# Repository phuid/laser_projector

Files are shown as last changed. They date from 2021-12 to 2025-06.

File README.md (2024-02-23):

# Raspberry Pi RGB laser projector
A vector laser projector with an easy to understand UI.\
UI includes:
- integrated display control with a rotary encoder,
- web server on the local network
- discord bot accesible when the RPi is online

## table of contents
- [Raspberry Pi RGB laser projector](#raspberry-pi-rgb-laser-projector)
  - [table of contents](#table-of-contents)
  - [thesis](#thesis)
  - [how to install](#how-to-install)
  - [supported projection file formats](#supported-projection-file-formats)
  - [hw](#hw)
    - [galvos](#galvos)
      - [DAC - mcp4822](#dac---mcp4822)
      - [amps - TL082](#amps---tl082)
    - [laser](#laser)
    - [LCD + encoder](#lcd--encoder)
  - [sw](#sw)
    - [communication](#communication)
    - [lasershow](#lasershow)
    - [UI](#ui)
    - [web\_ui](#web_ui)
    - [discord\_bot](#discord_bot)
    - [wifi\_manager](#wifi_manager)
    - [comms format](#comms-format)
      - [lasershow comms](#lasershow-comms)
        - [basic commands:](#basic-commands)
        - [responses:](#responses)
      - [wifi\_manager comms](#wifi_manager-comms)

## thesis
I wrote a whole thesis in [czech](https://en.wikipedia.org/wiki/Czech_Republic) language about this project. It is available in [this repository](https://github.com/phuid/laser_projector-thesis) [(direct link to the pdf file)](https://github.com/phuid/laser_projector-thesis/blob/master/text.pdf).

## how to install

```bash
git clone https://github.com/phuid/laser_projector.git
cd laser_projector
bash install.sh
```
this script installs all the dependencies of my programs and sets up the RaspberryPi to start all the programs on boot using [pm2](https://pm2.keymetrics.io/).

## supported projection file formats
The projector can read and project **.ild** and (much more popular) **.svg** file formats.
**.ild** files can be generated using specialised software like [laserworld showeditor](https://www.showeditor.com/en).
**.svg** files from any editor are internally converted to **.ild** using [this svg2ild.py script](https://github.com/marcan/openlase/blob/master/tools/svg2ild.py) from [gh/marcan/openlase](https://github.com/marcan/openlase)

## hw
My plans include battery power, usually galvos come with a power supply and powering the laser isn't that hard using a step-up. My module takes around 0.45A @ 9V. Make sure you dont brick your pi by taking its power. Raspberry Pis often don't take it well when an undervoltage occurs on their 5V line and they certainly aren't made to power anything more than an LED from their 3.3V PS.

### galvos
take -10 to +10V differential signal between to lines (base and inverted),
The DAC + opamps circuit which generates this signal is nicely described in [this article](https://www.instructables.com/Arduino-Laser-Show-With-Real-Galvos/).
My implemetation of it in kicad files can be found in [pcb/kicad](pcb/kicad).

#### DAC - mcp4822
DAC controlled by the RPi creates an analog signal between 0 and 5V.

#### amps - TL082
TL082 from texas instruments, each channel has one chip, each chip has two op amps.
One opamp inverts and modifies the signal based on the potenciometers (getting the inverted ILDA signal),
Second opamp inverts it again for the base ILDA signal

### laser
rgb laser module from https://www.laserlands.net/diode-laser-module/rgb-combined-white-laser-module/11010003.html
requires 8.5-12V power
takes 35kHz TTL / PWM on 3 pins, these pins are connected directly to the raspberry pi

pin connections between the laser module and RPi
|LASER|RPi|
|---|---|
|red|GPIO22|
|green|GPIO27|
|blue|GPIO17|

### LCD + encoder
Any 20x4 LCD with an I2C backpack + any rotary encoder with a button 
LCD connections:
|LCD|RPi|
|---|---|
|Vcc|5V|
|GND|GND|
|SCK|GPIO3|
|SDA|GPIO2|
|backlight|GPIO18|

encoder connections:
|encoder|RPi|
|---|---|
|A|GPIO5|
|common|GND|
|B|GPIO6|
|button1|GND|
|button1|GPIO13|

## sw
2 backend programs (lasershow *(c++)* + wifi_manager *(node.js)*) and 3 frontend programs (UI *(c++)* + web_ui *(node.js)* + discord_bot *(node.js)*)

### communication
each backend has its pub/sub sockets
lasershow publishes to `tcp://localhost:5556` and receives commands from `tcp://localhost:5556`
wifi_manager publishes to `tcp://localhost:5558` and receives commands from `tcp://localhost:5559`

### lasershow
- backend program that takes care of the actual projecting through controlling the galvos and the laser module

### UI
- allows control of backend programs through the built-in LCD and encoder

### web_ui
- allows control of backend programs through a web interface available on the local network

### discord_bot
- allows control of backend programs through a discord bot

### wifi_manager
- allows switching between three modes of wifi:
  - wifi off (`stealth`)
  - wifi on (`wifi`) -- RPi wifi on and trying to connect to known nearby networks
  - access point (`hotspot`) -- RPi wifi on transmitting its own wifi which other devices can connect to

### comms format
#### lasershow comms

lasershow executable takes commands **from all UI processes** through a **ZeroMQ TCP socket**
command format
`COMMAND` + ` ` + `ARG1` + ` ` + `ARG2` + ` ` + ` ` + `ARG4`
-> parse with a simple while loop lol no need for fancy functions

##### basic commands:
any process can send a command into the socket and all processes will read responses from lasershow executable
- `PROJECT` args: `<filename>`
  - `<filename>` must have extension `.ild`<!-- or `.lpc`(laserprojector_custom) --> otherwise error `INVALID_ARG`
- `STOP` (no args)
- `PAUSE` (no args)
- `GAME` args: `<game_name>`
  - `game_name` is any of the following ``//TODO: game names (not yes implemented)
- `PRESS` (no args), only handled if game is running
- `RELEASE` (no args), only handled if game is running
- `OPTION` args: `<mode>` `<option_name>` `<value>`
  - `mode`: any of `write`/`read`/`reset`
  - `option_name`: any of the following
    - `progress`
    - `current_frame` - if a projection is active, this will seek to the defined frame of the projection, must not exceed number_of_frames (every pos info gives this argument)
    - `point_delay`
    - `target_frame_time`
    - `repeat`
    - `trapeziod_horizontal`
    - `trapeziod_vertical`
  - `value` only read when using `write` parameter

##### responses:
lasershow exec can write to the socket at any time
- `ERROR: <e> <details>`:
  - `e`: any of the following; returned if received command couldn't be parsed correctly
    - `E2BIG`: too many arguments (option read/reset command probably includes value argument)
    - `EINVAL`: invalid argument (typo in argument or project filename probably has wrong extension)
    - `ENOENT`: file doesn't exist
    - `INVALID_CMD`: probably typo in a command
    - `OTHER`
  - `details`: if error type supports it, details will be included
- there is no success message
- `INFO: <details>`
  - details - one of following:
    - `OPTION <name> <val>`
      - name: name of option being changed; *any of*:
        - `point_delay`
        - `repeat`
        - `target_frame_time`
        - `trapezoid_horizontal`
        - `trapezoid_vertical`
      - val: numeric (float) value of the option
    - `STOP`
    - `PAUSE <val>`
      - val: 1 - paused, 0 - not paused
    - `PROJECT <filename>`
      - filename: filename of the file being projected
    - `POS <pos> OF <max>`
      - pos: position of coursor in projected file
      - max: size of projected file
- `DISPLAY: <text>`: client shall display text to the user and hide it when a new command comes or when user sees it
- `ALERT: <text>`: client shall display text to the user and only hide it and process following commands after user sees the alert

#### wifi_manager comms
takes following commands
- `read`: prints out following parameters:
  - `wifi_setting: <stealth|wifi|hotspot>`
  - `wifi_ssid: <SSID>`: SSID as returned by `iwgetid --raw` or `iw dev` in case hotspot is active
  - `mode_raw: <MODE_RAW>`: MODE_RAW (0-7) as returned by `iwgetid --mode --raw`
  - `mode: <MODE>`: MODE based on MODE_RAW; possible outputs: `Auto|Ad-Hoc|Managed|Master|Repeater|Secondary|Monitor|Unknown/bug`

- `write <stealth|wifi|hotspot>`
  - `stealth`: wifi off
  - `wifi`: connect to nearby known networks
  - `hotspot`: create new network, raspberry pi becomes the access point

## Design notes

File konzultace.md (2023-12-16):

# konzult

## hw
- rpi
- galva <- DAC 
- laser rgb <- DAC / TTL

### UI
- enkoder + OLED
- web_ui
- discord_bot

github haberturdeur /tet

## todo

- socket misto pipe (2.p.)

### done

- static encoder.hpp + cpp
- reference misto pointeru v menu_interract
- main menu def - constcast / std::string.c_str()

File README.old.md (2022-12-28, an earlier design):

# Raspberry Pi laser projector

not finished, not tested

## Table of contents

- [Raspberry Pi laser projector](#raspberry-pi-laser-projector)
  - [Table of contents](#table-of-contents)
  - [Tutorial](#tutorial)
    - [Hardware](#hardware)
    - [Software](#software)
      - [installing whole system from my disk image](#installing-whole-system-from-my-disk-image)
      - [installing executables from my repo source code](#installing-executables-from-my-repo-source-code)
        - [cloning my repository and installing manually](#cloning-my-repository-and-installing-manually)
    - [Hardware construction](#hardware-construction)
  - [What my code does - what happens when your RPI starts](#what-my-code-does---what-happens-when-your-rpi-starts)
  - [Progress (everything you need is above this part)](#progress-everything-you-need-is-above-this-part)
    - [Software progress](#software-progress)
    - [Hardware progress](#hardware-progress)

## Tutorial

*RPI = Raspberry Pi*
### Hardware

### Software

there are two ways of doing this, you can

- [install from a disk image](#installing-whole-system-from-my-disk-image)
  - much much easier
  - you need to download a 4GB file

  or

- [install the executables and dependencies yourself (download source)](#installing-executables-from-my-repo-source-code)
  - objectively harder
  - needs node and npm installed (i think node comes with the normal version of RPI OS preinstalled but i was using RPI OS Lite, since i needed to fit all this into a small .img file and was using a 4GB SD card)
    - **discord.js library requires node v16.6.0 or newer and npm v8.3.0 or newer**
    - using [Node version manager](https://github.com/nvm-sh/nvm) - [install tutorial](https://github.com/nvm-sh/nvm#installing-and-updating), [usage](https://github.com/nvm-sh/nvm#usage)
      - much more flexible
      - you can choose node and npm version
    - [download and install node and npm binaries yourself](https://www.makersupplies.sg/blogs/tutorials/how-to-install-node-js-and-npm-on-the-raspberry-pi)

#### installing whole system from my disk image

#### installing executables from my repo source code

##### cloning my repository and installing manually

download my code run these in the RPIs terminal

```console
git clone https://github.com/phuid/laser-projector.git
```

change your current working directory

```console
cd laser-projector
```

Install lasershow executable from [rpi-lasershow](https://github.com/tteskac/rpi-lasershow) project made by [@tteskac](https://github.com/tteskac)

enter rpi-lasershow dir

```console
cd rpi-lasershow
```

make the executable

```console
make
```

copy the executable to the main dir

```console
cp lasershow ../
```

exit the rpi-lasershow dir

```console
cd ..
```

at this point you dont really need the rpi-lasershow directory so you can delete it

it doesnt hurt to keep it at all this is just a possibility

```console
rm -r rpi-lasershow
```

now install the system dependencies and WiringPi and pm2
//TODO

then install all the node dependencies and set up pm2

enter every dir where a separate node server is gonna be located (**.**, **./discord_bot**, **./wifi_manager**) and intall its depencencies, then leave it

```console
npm i child_process http formidable fs path && pm2 start laser_projector-web-ui.js
``` 

**MAKE SURE, YOU CONNECTED THE AP/STEALTH/WIFI SWITCH CORRECTLY BEFORE STARTING THE wifi_manager.js SCRIPT, I DID IMPLEMENT A FAILSAFE, BUT EVEN I DONT REALLY TRUST IT (the failsafe includes the script not running if a pin isnt connected)

//TODO what fkin pin

```console
cd wifi_manager && npm i onoff child_process fs && pm2 start wifi_manager.js && cd ..
```

```console
cd discord_bot && npm i discord.js @discordjs/builders @discordjs/rest child_process path request fs
```

while you still are in **./discord_bot** you should put your bot credentials into config.json file and register the bots commands by running the deploy_commands.js script

```console
nano config.json
```

```console
node ./deploy_commands.js
```

now configure the pm2 autostart

```console
pm2 start discord_bot.js
```

then you can exit it

```console
cd ..
```

now check that all the pm2 services are online

```console
pm2 status
```

there should be three processes online like you can see below

//TODO

###### possible errors
if wifi manager isn't running and `pm2 logs wifi_manager` displays following
```js
/home/pi/laser_projector/wifi_manager/node_modules/bindings/bindings.js:121
        throw e;
        ^

Error: libnode.so.72: cannot open shared object file: No such file or directory
    at Object.Module._extensions..node (node:internal/modules/cjs/loader:1249:18)
    at Module.load (node:internal/modules/cjs/loader:1043:32)
    at Function.Module._load (node:internal/modules/cjs/loader:878:12)
    at Module.require (node:internal/modules/cjs/loader:1067:19)
    at require (node:internal/modules/cjs/helpers:103:18)
    at bindings (/home/pi/laser_projector/wifi_manager/node_modules/bindings/bindings.js:112:48)
    at /home/pi/laser_projector/wifi_manager/node_modules/epoll/epoll.js:7:31
    at Object.<anonymous> (/home/pi/laser_projector/wifi_manager/node_modules/epoll/epoll.js:15:3)
    at Module._compile (node:internal/modules/cjs/loader:1165:14)
    at Object.Module._extensions..js (node:internal/modules/cjs/loader:1219:10) {
  code: 'ERR_DLOPEN_FAILED'
}
```
run `cd wifi_manager/ && npm clean-install` in the laser_projector directory

### Hardware construction

this part is not gonna be added untill around Febuary 2022, since that's when my brother is gonna start working on modeling the case and when we are gonna buy the Galvos and all other components and put them together.

## What my code does - what happens when your RPI starts

1. pm2 starts ./laser_projector-web_ui.js, ./wifi_manage/wifi_manager.js and ./discord_bot/discord_bot.js

2. wifi_manager configures the wlan0 module based on the AP/stealth/wifi switch  

    *grounded = connected to ground*  
    *AP = access point (hotspot)*  

    1. if neither of pins (GPIO/BCM pin 6, GPIO/BCM pin 5) are grounded my code runs `sudo ifconfig wlan0 down`  
    and  
    `sudo systemctl disable hostapd dnsmasq`  
    else it runs just  
    `sudo ifconfig wlan0 up`

    2. if pin 6 is grounded it starts configuring an AP on the RPI

        1. `sudo systemctl enable hostapd dnsmasq`

        2. removes comment from the last section of my `/etc/dhcpcd.conf` file (add following to the file)  

                interface wlan0
                    static ip_address=192.168.4.1/24
                    nohook wpa_supplicant

        3. reboots the RPI

        4. every time it starts (on boot) it checks if hostapd.service is enabled
            - if it is NOT, it enables it in steps 1., 2. and 3. above
            - if it is, it continues

        5. `sudo ifdown wlan0`

        6. `sudo systemctl start dnsmasq`

        7. `sudo hostapd -B /etc/hostapd/hostapd.conf`

        8. `sudo systemctl reload dnsmasq`

    3. if pin 5 is grounded it starts configuring default wifi connection on the RPI
        1. `sudo systemctl stop hostapd dnsmasq`

        2. checks, if RPI is already connected to a wifi
            - if it is it breaks and doesnt continue
            - if it isn't it continues with steps 

        3. `sudo systemctl disable hostapd dnsmasq`

        4. comments out the last section of my `/etc/dhcpcd.conf` file

                #interface wlan0
                    #static ip_address=192.168.4.1/24
                    #nohook wpa_supplicant

        5. reboots the RPI and doesn't need to do anything after

## Progress (everything you need is above this part)

### Software progress

### Hardware progress

for some reason my pi saw the voltage on some pins as HIGH when they werent connected to anything, so i had to detect, wht pins were grounded instead of wht pins were taking power

still powered by usb
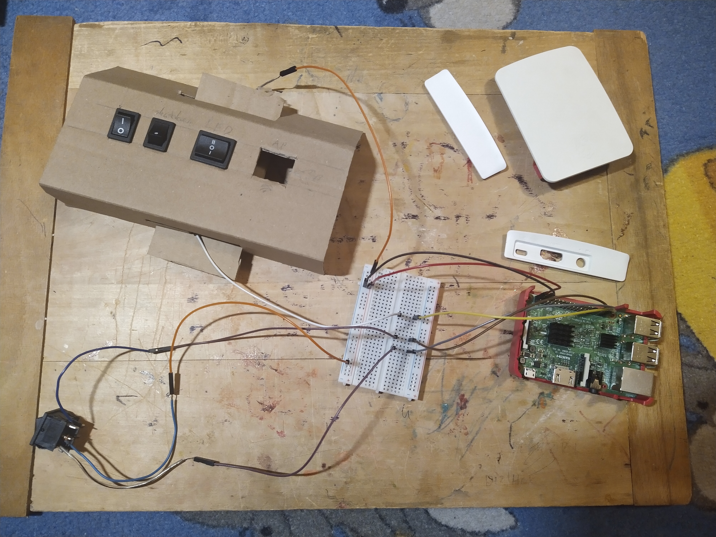
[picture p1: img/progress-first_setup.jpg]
first setup

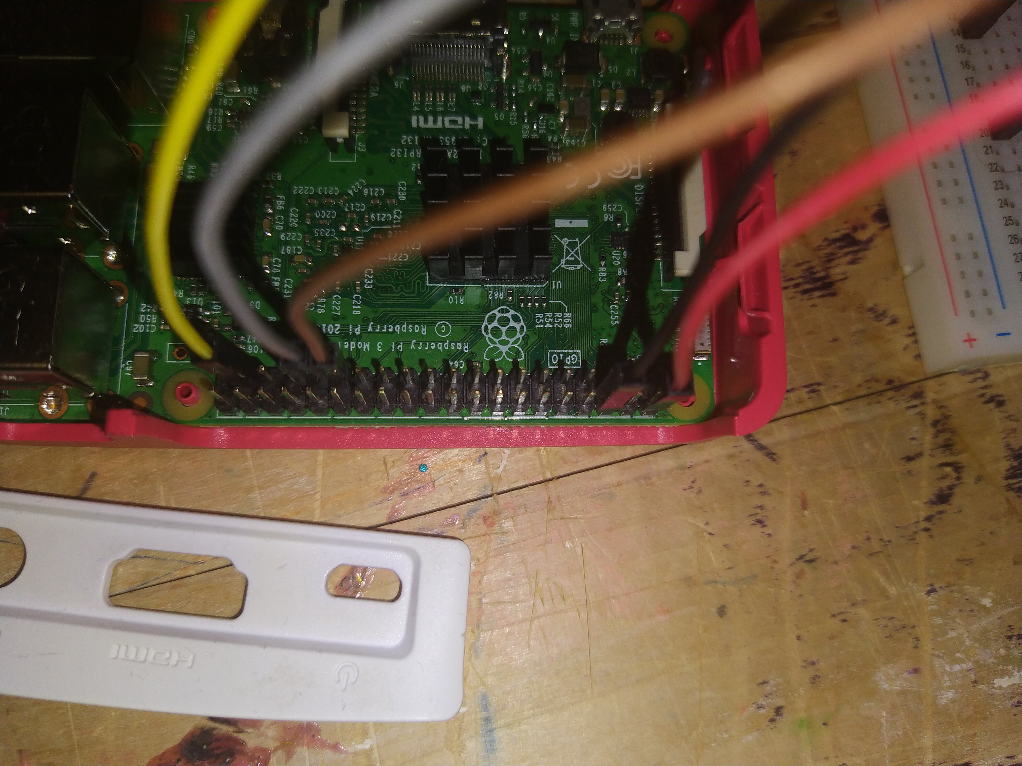
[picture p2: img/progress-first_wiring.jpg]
first wiring


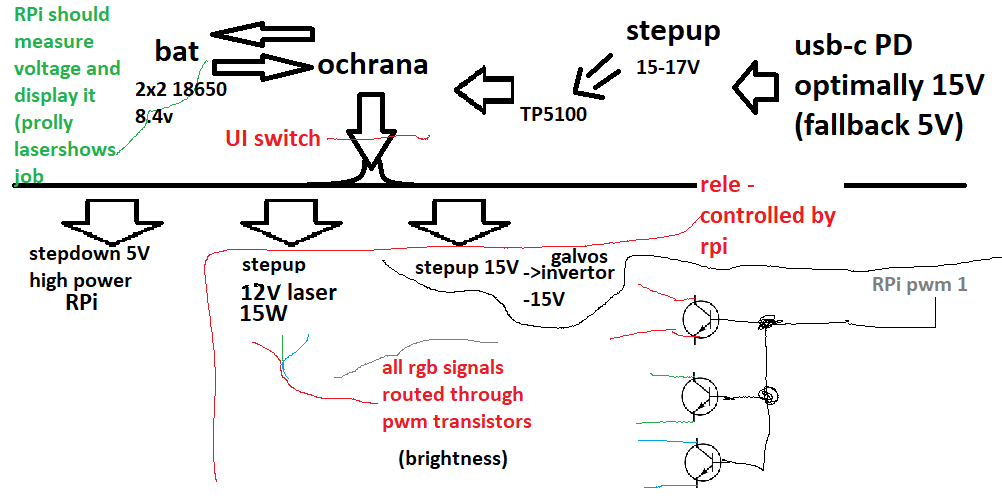
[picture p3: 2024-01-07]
hw_napajeni_schema.png

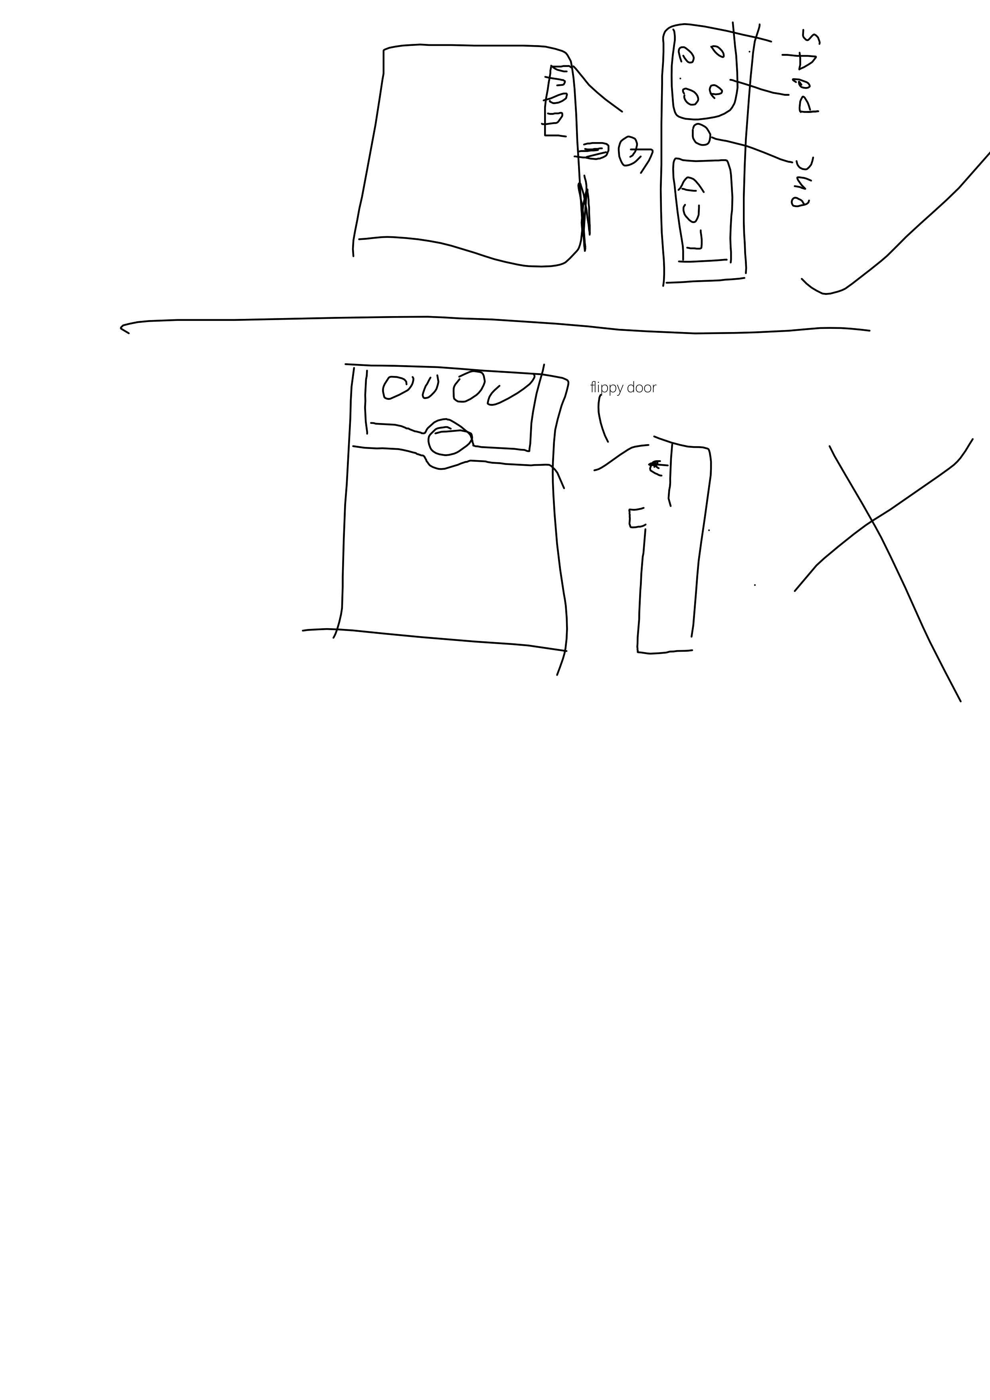
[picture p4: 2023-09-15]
pcb/yup.png

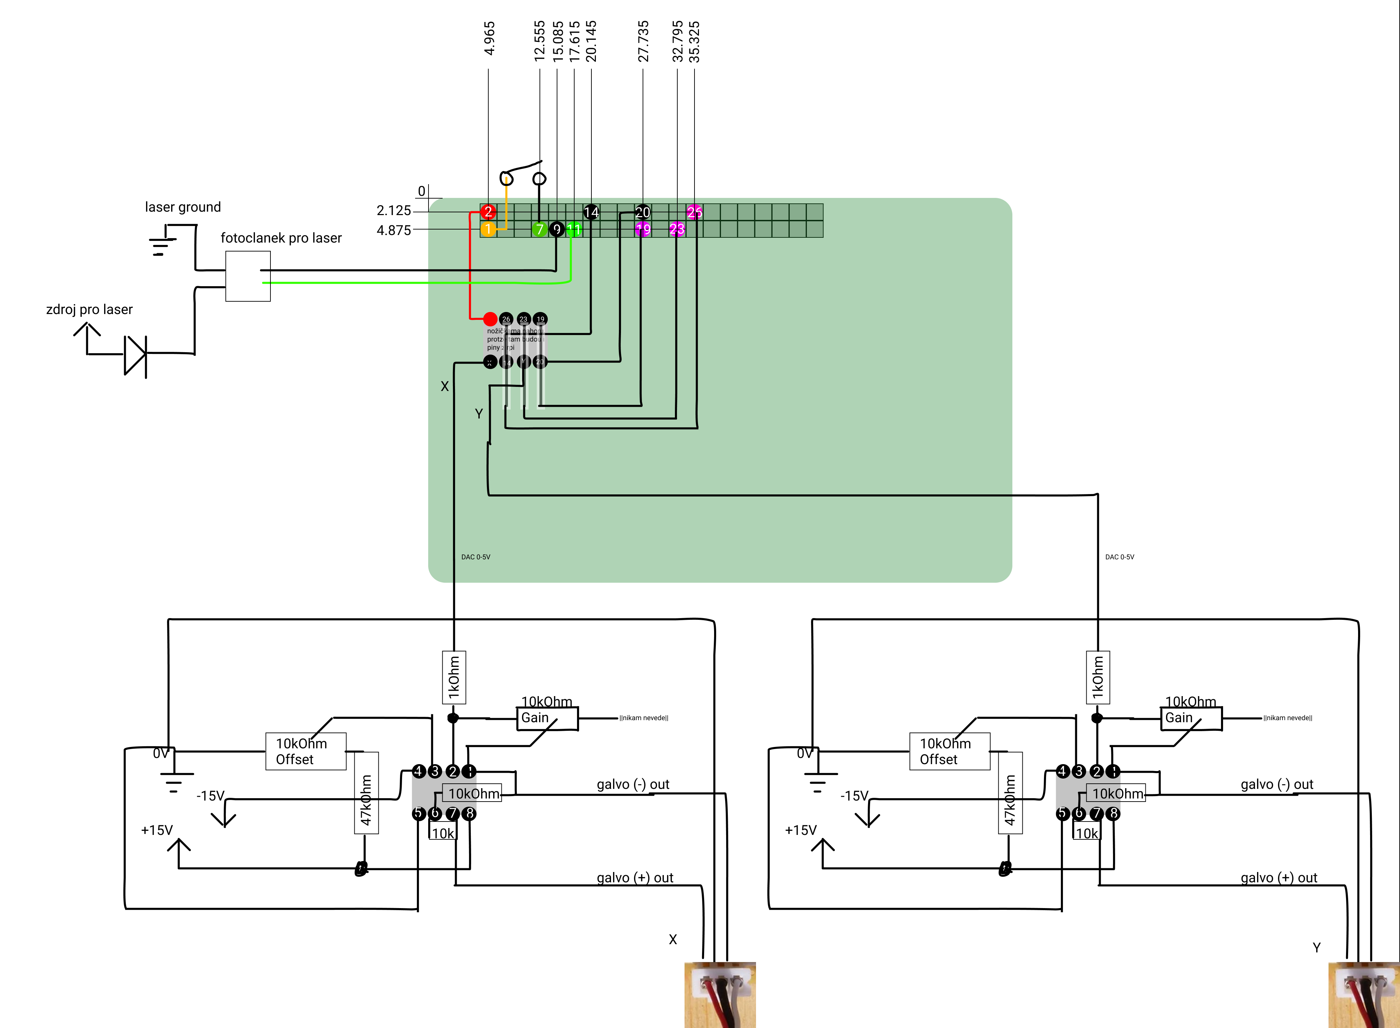
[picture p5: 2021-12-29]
pcb/rpi laser projector.png

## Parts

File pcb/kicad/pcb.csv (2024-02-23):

Source: | C:\Users\simon\random_code\_projects\laser_projector\pcb\kicad\pcb.kicad_sch
Date: | 02/10/2022 14:52:29
Tool: | Eeschema (6.0.5)
Generator: | C:\Program Files\KiCad\6.0\bin\scripting\plugins/bom_csv_grouped_by_value.py
Component Count: | 23
Individual Components:
Item | Qty | Reference(s) | Value | LibPart | Footprint | Datasheet
 |  | buttons1 | Conn_01x04_Male | Connector:Conn_01x04_Male | Connector_PinHeader_2.54mm:PinHeader_1x04_P2.54mm_Horizontal | ~
 |  | galX1 | Conn_01x03_Male | Connector:Conn_01x03_Male | Connector_PinHeader_2.54mm:PinHeader_1x03_P2.54mm_Horizontal | ~
 |  | galY1 | Conn_01x03_Male | Connector:Conn_01x03_Male | Connector_PinHeader_2.54mm:PinHeader_1x03_P2.54mm_Horizontal | ~
 |  | J1 | Raspberry_Pi_2_3 | Connector:Raspberry_Pi_2_3 | Connector_PinSocket_2.54mm:PinSocket_2x20_P2.54mm_Vertical | https://www.raspberrypi.org/documentation/hardware/raspberrypi/schematics/rpi_SCH_3bplus_1p0_reduced.pdf
 |  | laser1 | Conn_01x02_Male | Connector:Conn_01x02_Male | Connector_PinHeader_2.54mm:PinHeader_1x02_P2.54mm_Horizontal | ~
 |  | R1 | 1kR | Device:R | Resistor_THT:R_Axial_DIN0207_L6.3mm_D2.5mm_P10.16mm_Horizontal | ~
 |  | R4 | 47kR | Device:R | Resistor_THT:R_Axial_DIN0207_L6.3mm_D2.5mm_P10.16mm_Horizontal | ~
 |  | R5 | 10kR | Device:R | Resistor_THT:R_Axial_DIN0207_L6.3mm_D2.5mm_P10.16mm_Horizontal | ~
 |  | R6 | 10kR | Device:R | Resistor_THT:R_Axial_DIN0207_L6.3mm_D2.5mm_P10.16mm_Horizontal | ~
 |  | R7 | 1kR | Device:R | Resistor_THT:R_Axial_DIN0207_L6.3mm_D2.5mm_P10.16mm_Horizontal | ~
 |  | R9 | 47kR | Device:R | Resistor_THT:R_Axial_DIN0207_L6.3mm_D2.5mm_P10.16mm_Horizontal | ~
 |  | R11 | 10kR | Device:R | Resistor_THT:R_Axial_DIN0207_L6.3mm_D2.5mm_P10.16mm_Horizontal | ~
 |  | R12 | 10kR | Device:R | Resistor_THT:R_Axial_DIN0207_L6.3mm_D2.5mm_P10.16mm_Horizontal | ~
 |  | RLED1 | 510R | Device:R | Resistor_THT:R_Axial_DIN0207_L6.3mm_D2.5mm_P10.16mm_Horizontal | ~
 |  | U1 | MCP4822 | Analog_DAC:MCP4822 | Package_DIP:DIP-8_W7.62mm | http://ww1.microchip.com/downloads/en/DeviceDoc/20002249B.pdf
 |  | U2 | TL082 | Amplifier_Operational:TL082 | Package_DIP:DIP-8_W7.62mm | http://www.ti.com/lit/ds/symlink/tl081.pdf
 |  | U3 | TL082 | Amplifier_Operational:TL082 | Package_DIP:DIP-8_W7.62mm | http://www.ti.com/lit/ds/symlink/tl081.pdf
 |  | U4 | ASSR-1218 | Relay_SolidState:ASSR-1218 | Package_DIP:DIP-4_W7.62mm | https://docs.broadcom.com/docs/AV02-0173EN
 |  | Vi1 | Conn_01x03_Male | Connector:Conn_01x03_Male | Connector_PinHeader_2.54mm:PinHeader_1x03_P2.54mm_Horizontal | ~
 |  | Xgain1 | 10kR | pcb-rescue:R_POT-Device | Potentiometer_THT:Potentiometer_Alps_RK09K_Single_Vertical
 |  | Xoffset1 | 10kR | pcb-rescue:R_POT-Device | Potentiometer_THT:Potentiometer_Alps_RK09K_Single_Vertical
 |  | Ygain1 | 10kR | pcb-rescue:R_POT-Device | Potentiometer_THT:Potentiometer_Alps_RK09K_Single_Vertical
 |  | Yoffset1 | 10kR | pcb-rescue:R_POT-Device | Potentiometer_THT:Potentiometer_Alps_RK09K_Single_Vertical
Collated Components:
Item | Qty | Reference(s) | Value | LibPart | Footprint | Datasheet
1 | 1 | buttons1 | Conn_01x04_Male | Connector:Conn_01x04_Male | Connector_PinHeader_2.54mm:PinHeader_1x04_P2.54mm_Horizontal | ~
2 | 3 | galX1, galY1, Vi1 | Conn_01x03_Male | Connector:Conn_01x03_Male | Connector_PinHeader_2.54mm:PinHeader_1x03_P2.54mm_Horizontal | ~
3 | 1 | J1 | Raspberry_Pi_2_3 | Connector:Raspberry_Pi_2_3 | Connector_PinSocket_2.54mm:PinSocket_2x20_P2.54mm_Vertical | https://www.raspberrypi.org/documentation/hardware/raspberrypi/schematics/rpi_SCH_3bplus_1p0_reduced.pdf
4 | 1 | laser1 | Conn_01x02_Male | Connector:Conn_01x02_Male | Connector_PinHeader_2.54mm:PinHeader_1x02_P2.54mm_Horizontal | ~
5 | 2 | R1, R7 | 1kR | Device:R | Resistor_THT:R_Axial_DIN0207_L6.3mm_D2.5mm_P10.16mm_Horizontal | ~
6 | 2 | R4, R9 | 47kR | Device:R | Resistor_THT:R_Axial_DIN0207_L6.3mm_D2.5mm_P10.16mm_Horizontal | ~
7 | 4 | R5, R6, R11, R12 | 10kR | Device:R | Resistor_THT:R_Axial_DIN0207_L6.3mm_D2.5mm_P10.16mm_Horizontal | ~
8 | 1 | RLED1 | 510R | Device:R | Resistor_THT:R_Axial_DIN0207_L6.3mm_D2.5mm_P10.16mm_Horizontal | ~
9 | 1 | U1 | MCP4822 | Analog_DAC:MCP4822 | Package_DIP:DIP-8_W7.62mm | http://ww1.microchip.com/downloads/en/DeviceDoc/20002249B.pdf
10 | 2 | U2, U3 | TL082 | Amplifier_Operational:TL082 | Package_DIP:DIP-8_W7.62mm | http://www.ti.com/lit/ds/symlink/tl081.pdf
11 | 1 | U4 | ASSR-1218 | Relay_SolidState:ASSR-1218 | Package_DIP:DIP-4_W7.62mm | https://docs.broadcom.com/docs/AV02-0173EN
12 | 4 | Xgain1, Xoffset1, Ygain1, Yoffset1 | 10kR | pcb-rescue:R_POT-Device | Potentiometer_THT:Potentiometer_Alps_RK09K_Single_Vertical

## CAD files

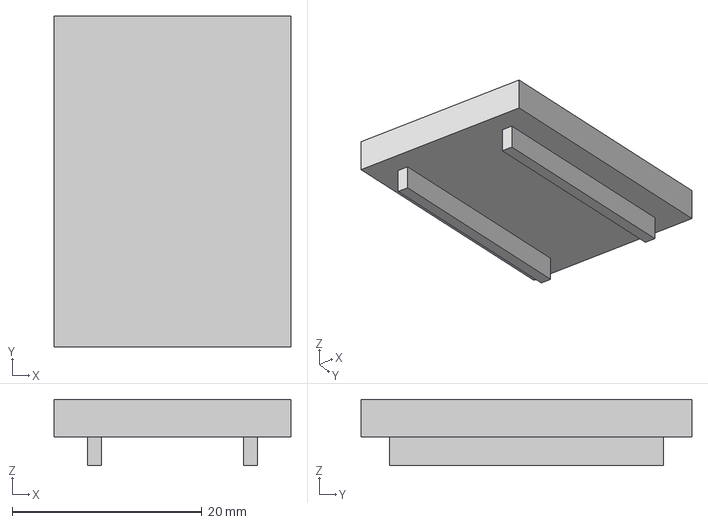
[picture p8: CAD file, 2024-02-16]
case-3D/laser_projector_3d_files/encoder_hold.3mf
24.9 x 34.8 x 7.00 mm

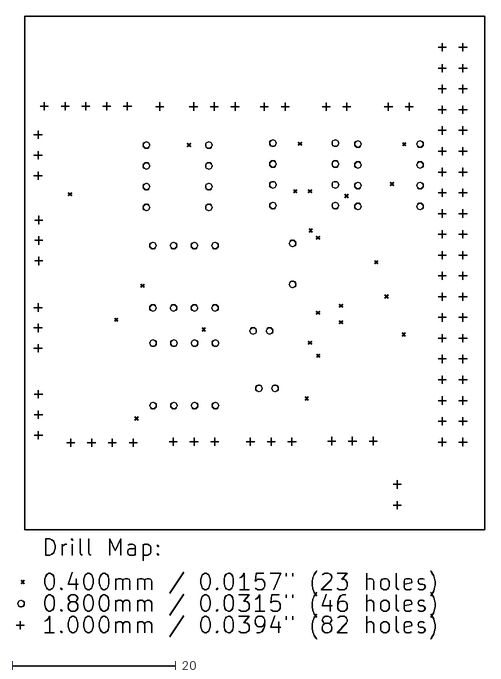
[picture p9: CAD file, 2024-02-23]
pcb/kicad/gerber/pcb-drl_map.dxf
57.3 x 76.2

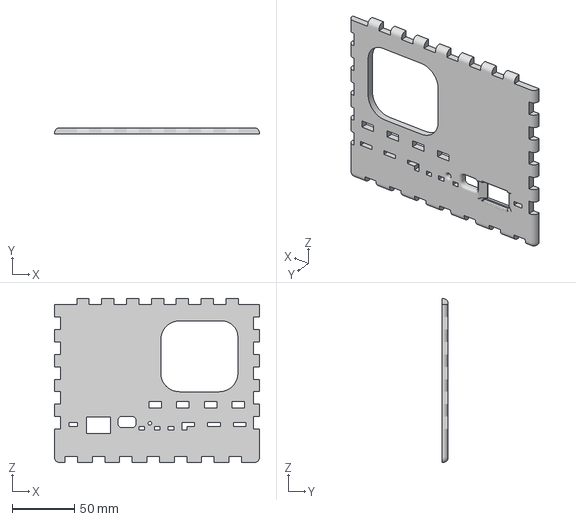
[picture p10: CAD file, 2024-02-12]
case-3D/laser_projector_3d_files/newcase_laser_projector v55_side3.3mf
165.0 x 5.00 x 132.0 mm

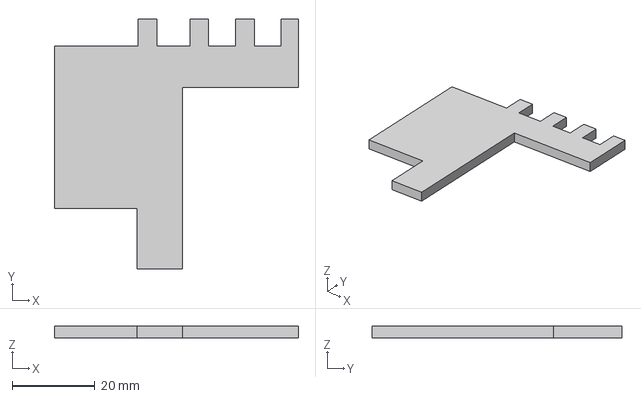
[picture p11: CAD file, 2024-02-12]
case-3D/laser_projector_3d_files/newcase_laser_projector v55_layer0-glueon.3mf
58.8 x 60.2 x 3.00 mm

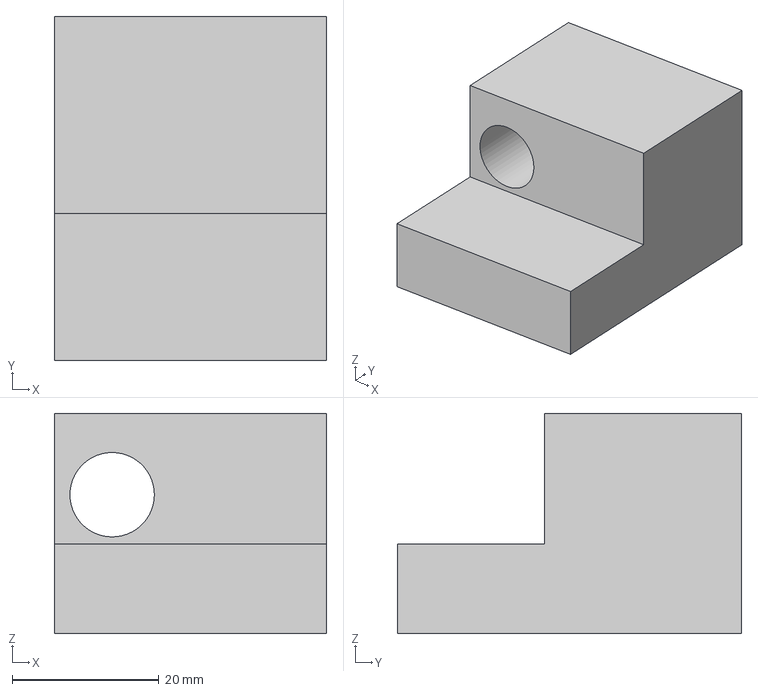
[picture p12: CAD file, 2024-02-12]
case-3D/laser_projector_3d_files/low_laser_hold.3mf
37.1 x 46.9 x 30.0 mm

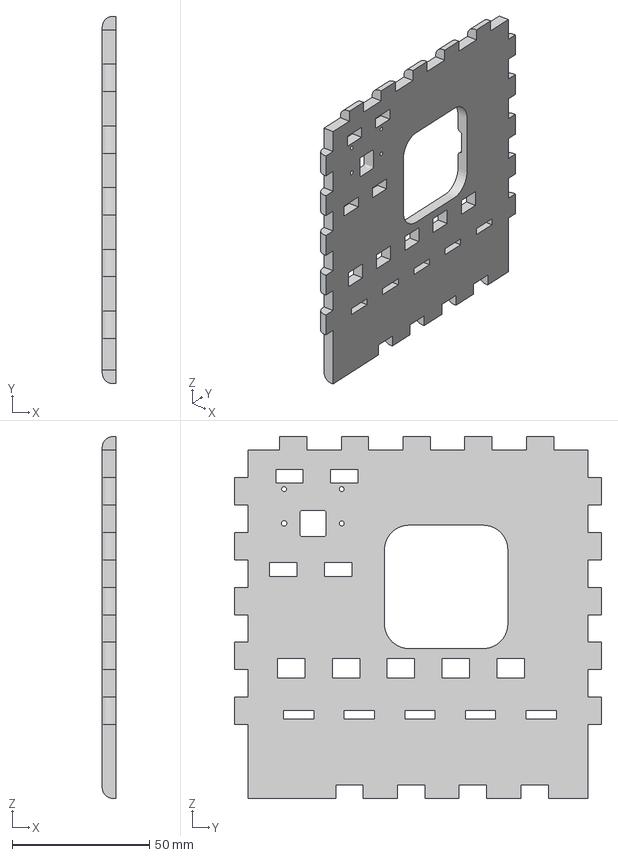
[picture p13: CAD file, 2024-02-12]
case-3D/laser_projector_3d_files/newcase_laser_projector v55_side1.3mf
5.00 x 134.0 x 132.0 mm

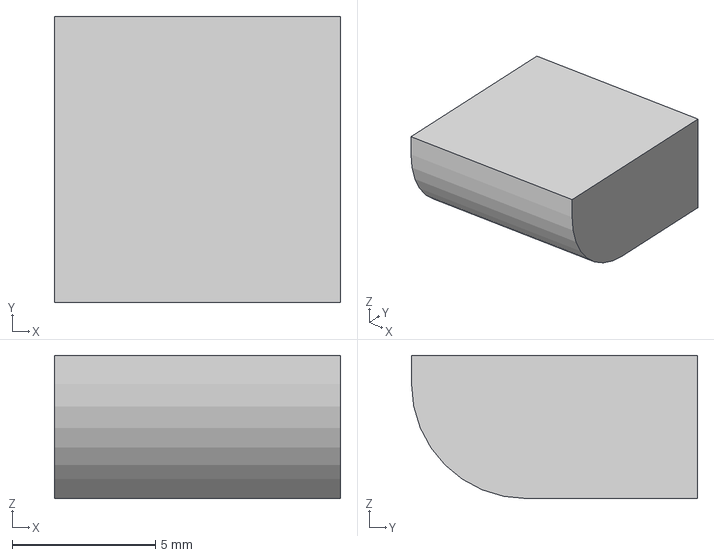
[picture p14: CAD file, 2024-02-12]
case-3D/laser_projector_3d_files/newcase_laser_projector v55_19x_bottom_hold_body.3mf
10.0 x 10.0 x 5.00 mm

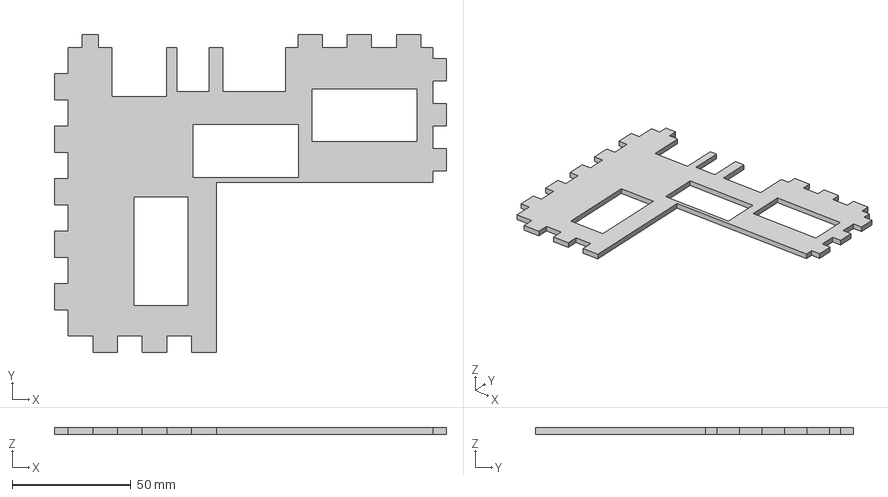
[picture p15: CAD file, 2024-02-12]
case-3D/laser_projector_3d_files/newcase_laser_projector v55_layer0.3mf
165.1 x 134.0 x 3.00 mm

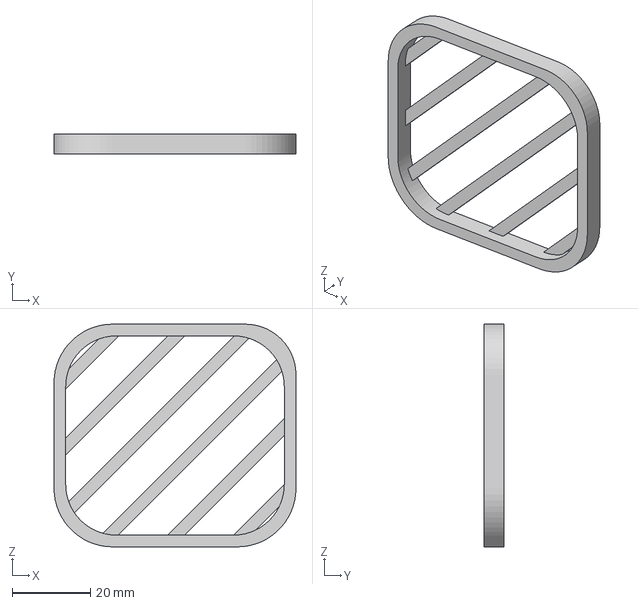
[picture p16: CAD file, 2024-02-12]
case-3D/laser_projector_3d_files/newcase_laser_projector v55_fan_cover.3mf
62.0 x 5.00 x 57.1 mm

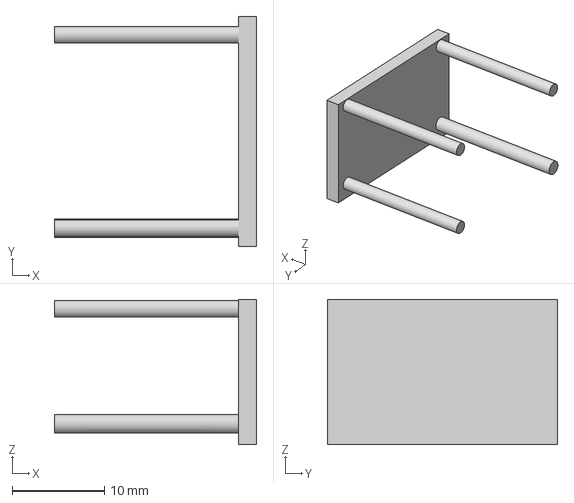
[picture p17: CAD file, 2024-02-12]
case-3D/laser_projector_3d_files/camera_hold.3mf
22.0 x 25.0 x 15.8 mm

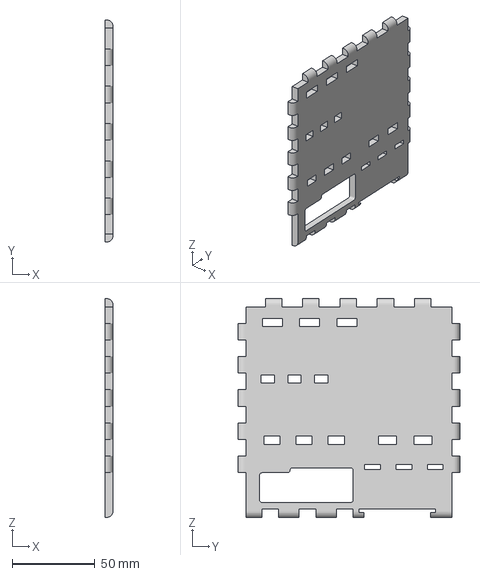
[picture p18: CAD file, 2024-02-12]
case-3D/laser_projector_3d_files/newcase_laser_projector v55_side0.3mf
5.00 x 134.0 x 132.0 mm

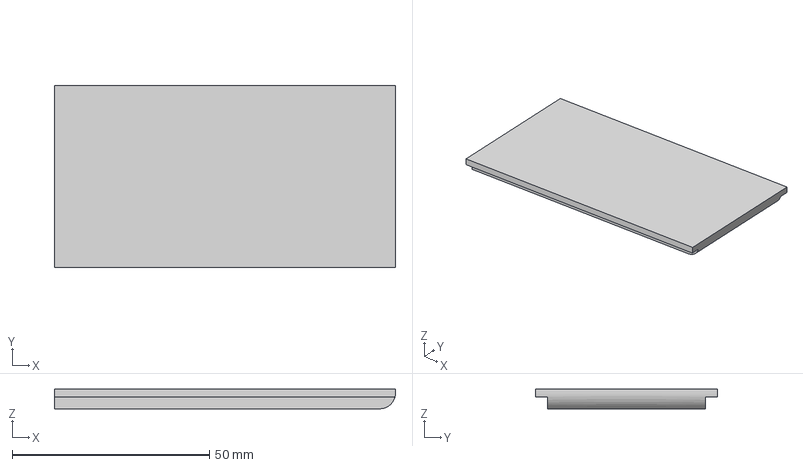
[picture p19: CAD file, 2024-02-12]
case-3D/laser_projector_3d_files/newcase_laser_projector v55_bat_cover1.3mf
86.3 x 46.0 x 5.00 mm

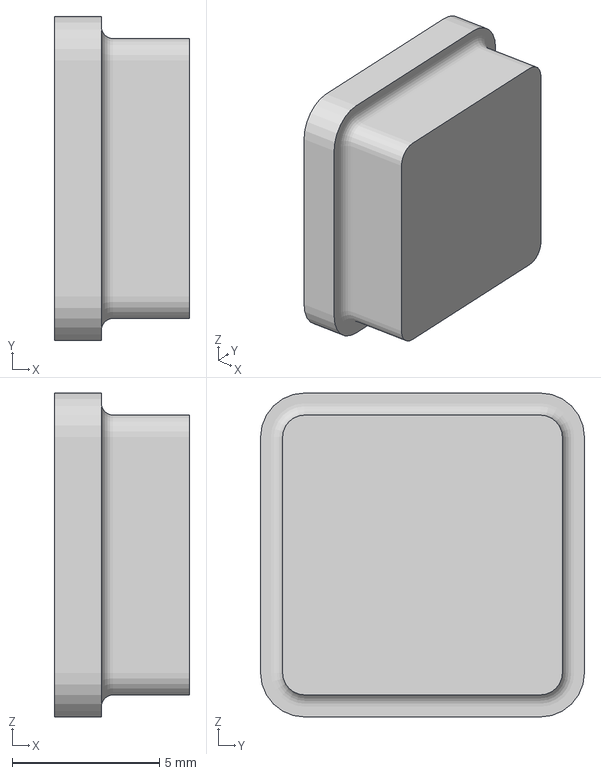
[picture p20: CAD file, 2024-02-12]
case-3D/laser_projector_3d_files/newcase_laser_projector v55_camera_cover.3mf
4.60 x 11.0 x 11.0 mm

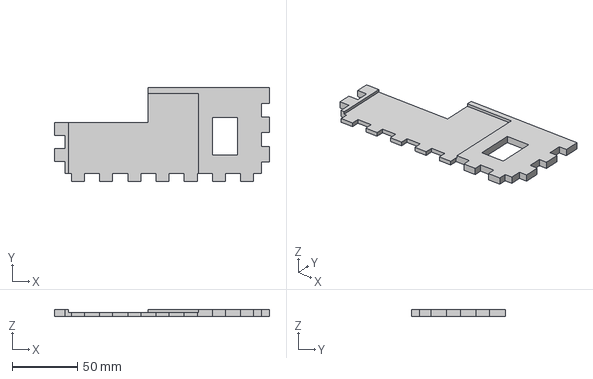
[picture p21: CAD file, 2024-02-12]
case-3D/laser_projector_3d_files/newcase_laser_projector v55_layer3.3mf
165.0 x 71.8 x 5.00 mm

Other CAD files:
case-3D/laser_projector_3d_files/Knob_6.3.stl
case-3D/laser_projector_3d_files/newcase_laser_projector v55_top.3mf
case-3D/laser_projector_3d_files/newcase_laser_projector v55_layer2.3mf
case-3D/laser_projector_3d_files/newcase_laser_projector v55_layer1.3mf
case-3D/laser_projector_3d_files/bat_cover_hold (1).3mf
case-3D/laser_projector_3d_files/bat_cover_hold.3mf
case-3D/laser_projector_3d_files/newcase_laser_projector v55_bat_cover.3mf
case-3D/laser_projector_3d_files/newcase_laser_projector v55_batprotec_hold.3mf
case-3D/laser_projector_3d_files/newcase_laser_projector v55_bottom.3mf
case-3D/laser_projector_3d_files/newcase_laser_projector v55_camera_hold.3mf
case-3D/laser_projector_3d_files/newcase_laser_projector v55_galvo_cover.3mf
case-3D/laser_projector_3d_files/newcase_laser_projector v55_pot_cover.3mf
case-3D/laser_projector_3d_files/newcase_laser_projector v55_side2.3mf

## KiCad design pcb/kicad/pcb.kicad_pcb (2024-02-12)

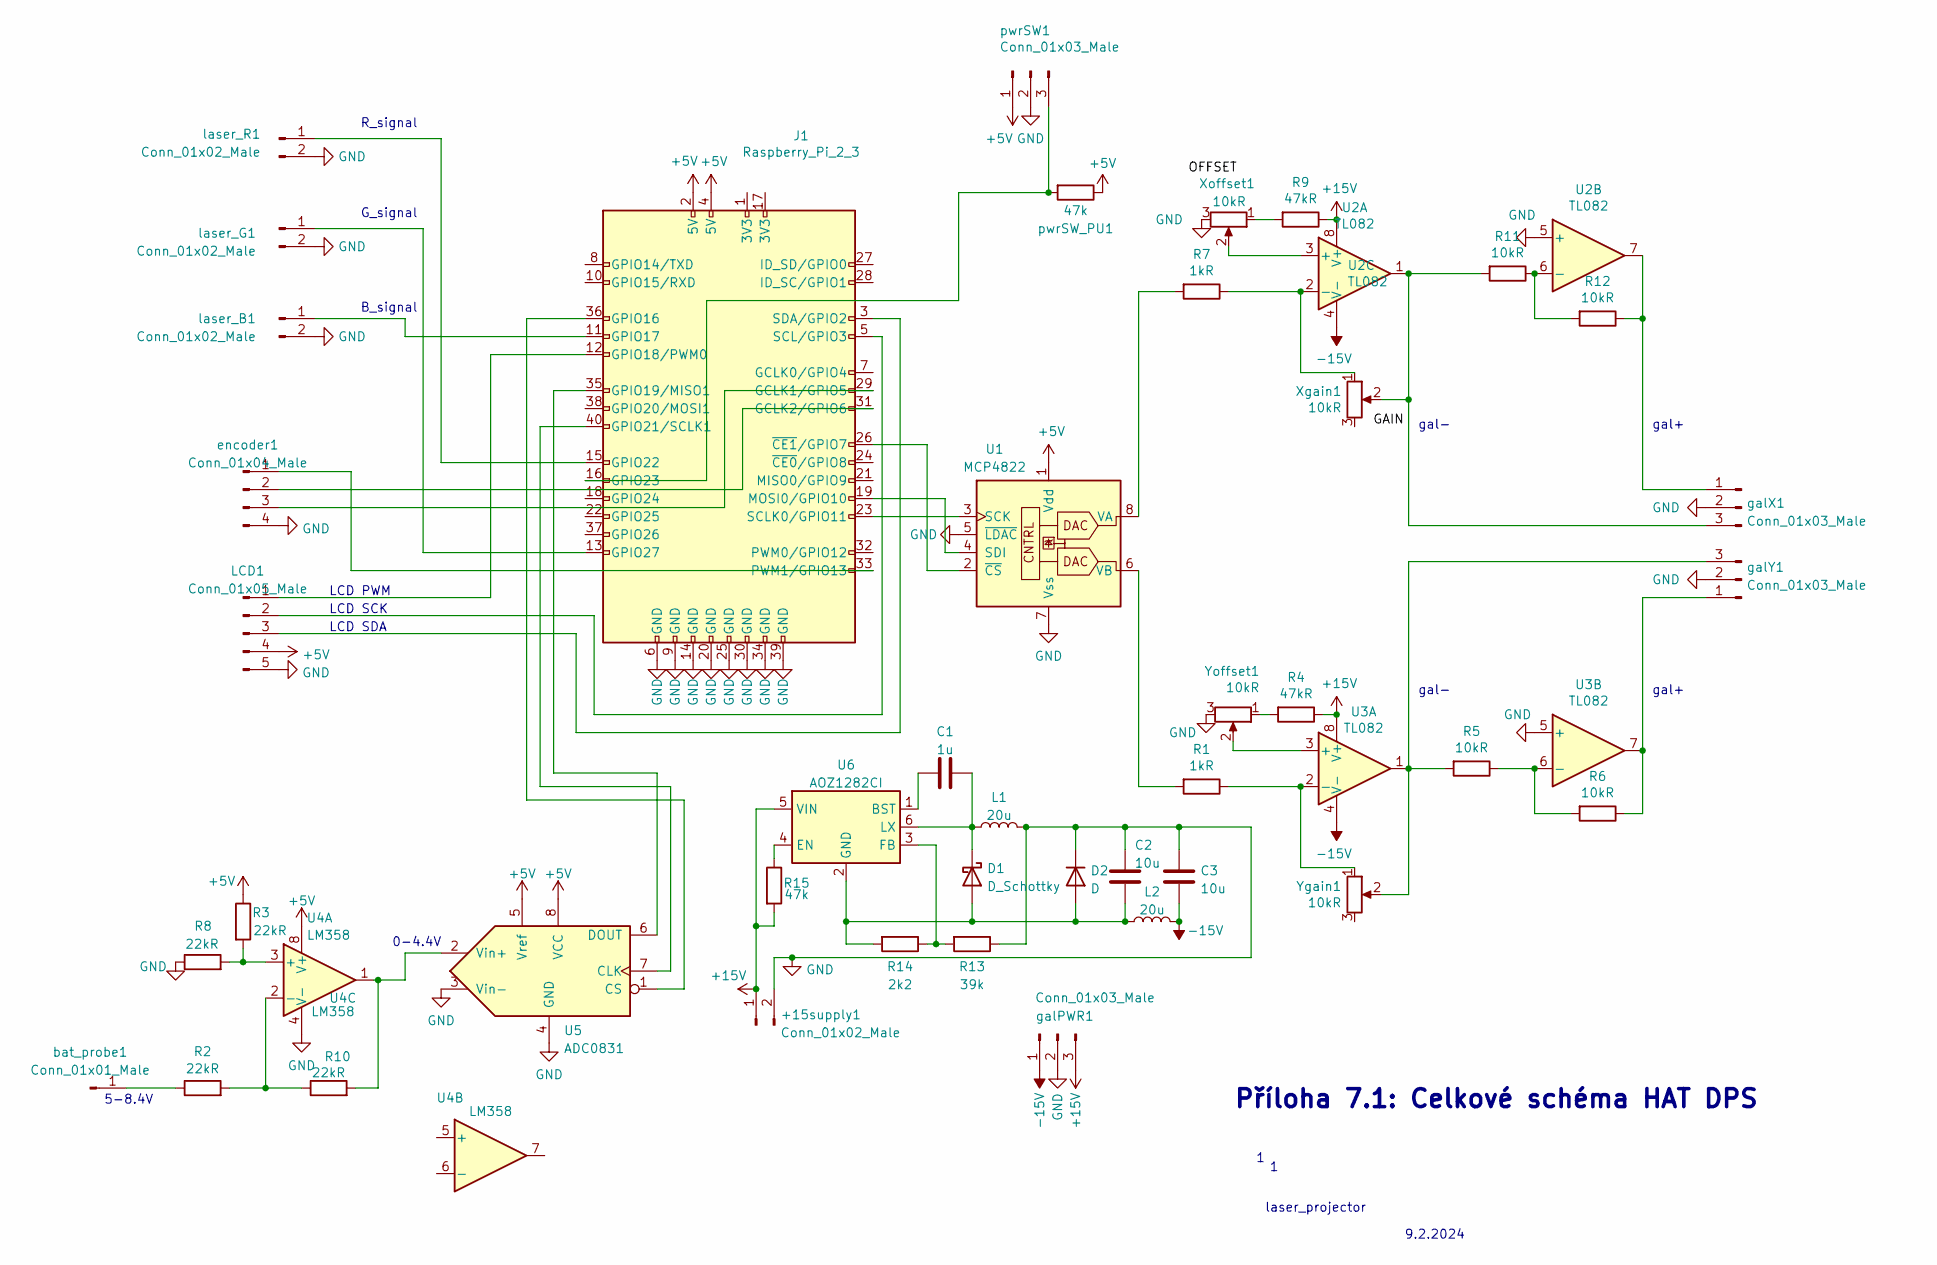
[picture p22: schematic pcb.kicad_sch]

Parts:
+15supply1: Conn_01x02_Male; PinHeader_1x02_P2.54mm_Horizontal
C1: 1u; C_Disc_D5.0mm_W2.5mm_P5.00mm
C2, C3: 10u; CP_Radial_D5.0mm_P2.00mm
D1: D_Schottky; D_SMC_Handsoldering
D2: D; D_SMC_Handsoldering
J1: Raspberry_Pi_2_3; PinSocket_2x20_P2.54mm_Vertical
L1, L2: 20u; L_Sumida_CR75
LCD1: Conn_01x05_Male; PinHeader_1x05_P2.54mm_Horizontal
R1, R7: 1kR; R_1812_4532Metric_Pad1.30x3.40mm_HandSolder
R2, R3, R8, R10: 22kR; R_1812_4532Metric_Pad1.30x3.40mm_HandSolder
R4, R9: 47kR; R_1812_4532Metric_Pad1.30x3.40mm_HandSolder
R5, R6, R11, R12: 10kR; R_1812_4532Metric_Pad1.30x3.40mm_HandSolder
R13: 39k; R_1812_4532Metric_Pad1.30x3.40mm_HandSolder
R14: 2k2; R_1812_4532Metric_Pad1.30x3.40mm_HandSolder
R15: 47k; R_1812_4532Metric_Pad1.30x3.40mm_HandSolder
U1: MCP4822; DIP-8_W7.62mm
U2, U3: TL082; DIP-8_W7.62mm
U4: LM358; DIP-8_W7.62mm
U5: ADC0831; DIP-8_W7.62mm
U6: AOZ1282CI; SOT-23-6
Xgain1: 10kR; Potentiometer_Alps_RK09K_Single_Vertical
Xoffset1: 10kR; Potentiometer_Alps_RK09K_Single_Vertical
Ygain1: 10kR; Potentiometer_Alps_RK09K_Single_Vertical
Yoffset1: 10kR; Potentiometer_Alps_RK09K_Single_Vertical
bat_probe1: Conn_01x01_Male; PinHeader_1x01_P2.54mm_Horizontal
encoder1: Conn_01x04_Male; PinHeader_1x04_P2.54mm_Horizontal
galPWR1: Conn_01x03_Male; PinHeader_1x03_P2.54mm_Horizontal
galX1: Conn_01x03_Male; PinHeader_1x03_P2.54mm_Horizontal
galY1: Conn_01x03_Male; PinHeader_1x03_P2.54mm_Horizontal
laser_B1: Conn_01x02_Male; PinHeader_1x02_P2.54mm_Horizontal
laser_G1: Conn_01x02_Male; PinHeader_1x02_P2.54mm_Horizontal
laser_R1: Conn_01x02_Male; PinHeader_1x02_P2.54mm_Horizontal
pwrSW1: Conn_01x03_Male; PinHeader_1x03_P2.54mm_Horizontal
pwrSW_PU1: 47k; R_1812_4532Metric_Pad1.30x3.40mm_HandSolder

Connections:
+5V: J1.2 (5V), J1.4 (5V), LCD1.4, R3.1, U1.1 (Vdd), U4.8 (V+), U5.5 (Vref), U5.8 (VCC), pwrSW1.1, pwrSW_PU1.1
+15V: +15supply1.1, R4.1, R9.1, R15.2, U2.8 (V+), U3.8 (V+), U6.5 (VIN), galPWR1.3
-15V: C3.2, L2.2, U2.4 (V-), U3.4 (V-), galPWR1.1
GND: +15supply1.2, C2.1, C3.1, D2.1 (K), J1.6 (GND), J1.9 (GND), J1.14 (GND), J1.20 (GND), J1.25 (GND), J1.30 (GND), J1.34 (GND), J1.39 (GND), L1.2, LCD1.5, R8.1, R13.1, U1.5 (~LDAC), U1.7 (Vss), U2.5 (+), U3.5 (+), U4.4 (V-), U5.3 (Vin-), U5.4 (GND), Xoffset1.3, Yoffset1.3, encoder1.4, galPWR1.2, galX1.2, galY1.2, laser_B1.2, laser_G1.2, laser_R1.2, pwrSW1.2
unnamed: C2.2, D1.2 (A), D2.2 (A), L2.1, R14.2, U6.2 (GND)
unnamed: C1.1, D1.1 (K), L1.1, U6.6 (LX)
unnamed: J1.29 (GCLK1/GPIO5), encoder1.3
unnamed: J1.31 (GCLK2/GPIO6), encoder1.2
unnamed: J1.36 (GPIO16), U5.1 (CS)
unnamed: J1.11 (GPIO17), laser_B1.1
unnamed: J1.12 (GPIO18/PWM0), LCD1.1
unnamed: J1.35 (GPIO19/MISO1), U5.6 (DOUT)
unnamed: J1.40 (GPIO21/SCLK1), U5.7 (CLK)
unnamed: J1.15 (GPIO22), laser_R1.1
unnamed: J1.16 (GPIO23), pwrSW1.3, pwrSW_PU1.2
unnamed: J1.13 (GPIO27), laser_G1.1
unnamed: J1.19 (MOSI0/GPIO10), U1.4 (SDI)
unnamed: J1.33 (PWM1/GPIO13), encoder1.1
unnamed: J1.23 (SCLK0/GPIO11), U1.3 (SCK)
unnamed: J1.5 (SCL/GPIO3), LCD1.2
unnamed: J1.3 (SDA/GPIO2), LCD1.3
unnamed: J1.26 (~CE1/GPIO7), U1.2 (~CS)
unnamed: R4.2, Yoffset1.1
unnamed: R9.2, Xoffset1.1
unnamed: R7.2, U1.8 (VA)
unnamed: R1.2, U1.6 (VB)
unnamed: U2.3 (+), Xoffset1.2
unnamed: R7.1, U2.2 (-), Xgain1.1
unnamed: R11.1, R12.2, U2.6 (-)
unnamed: U3.3 (+), Yoffset1.2
unnamed: R1.1, U3.2 (-), Ygain1.1
unnamed: R5.1, R6.2, U3.6 (-)
unnamed: R3.2, R8.2, U4.3 (+)
unnamed: R2.2, R10.1, U4.2 (-)
unnamed: R10.2, U4.1, U5.2 (Vin+)
unnamed: C1.2, U6.1 (BST)
unnamed: R15.1, U6.4 (EN)
unnamed: R13.2, R14.1, U6.3 (FB)
unnamed: R2.1, bat_probe1.1
unnamed: R12.1, U2.7, galX1.1
unnamed: R11.2, U2.1, Xgain1.2, galX1.3
unnamed: R6.1, U3.7, galY1.1
unnamed: R5.2, U3.1, Ygain1.2, galY1.3

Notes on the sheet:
Příloha 7.1: Celkové schéma HAT DPS
LCD SCK
G_signal
0-4.4V
LCD PWM
gal-
9.2.2024
B_signal
LCD SDA
laser_projector
R_signal
gal+
5-8.4V

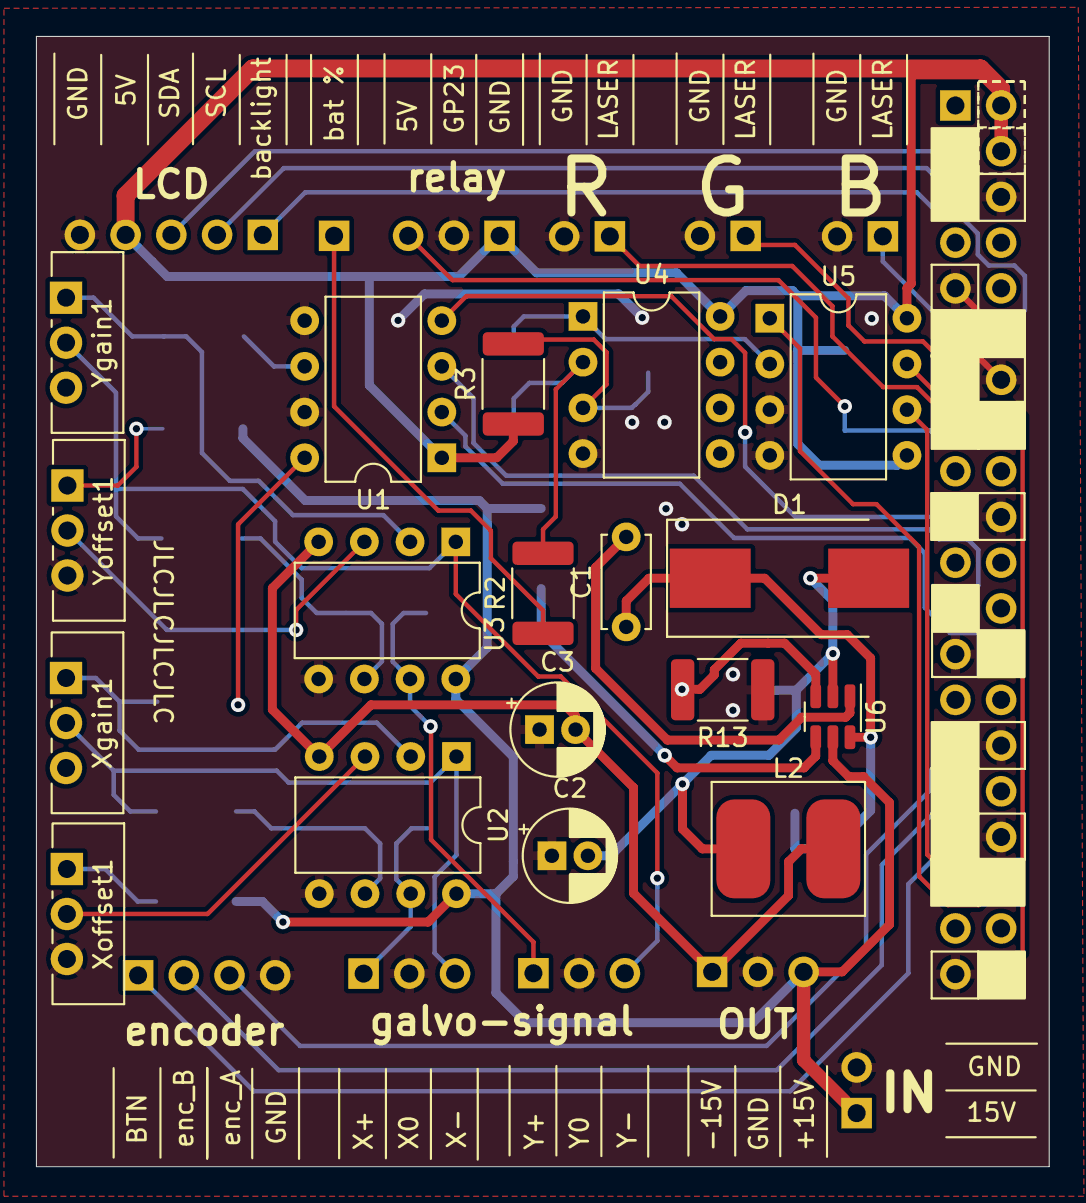
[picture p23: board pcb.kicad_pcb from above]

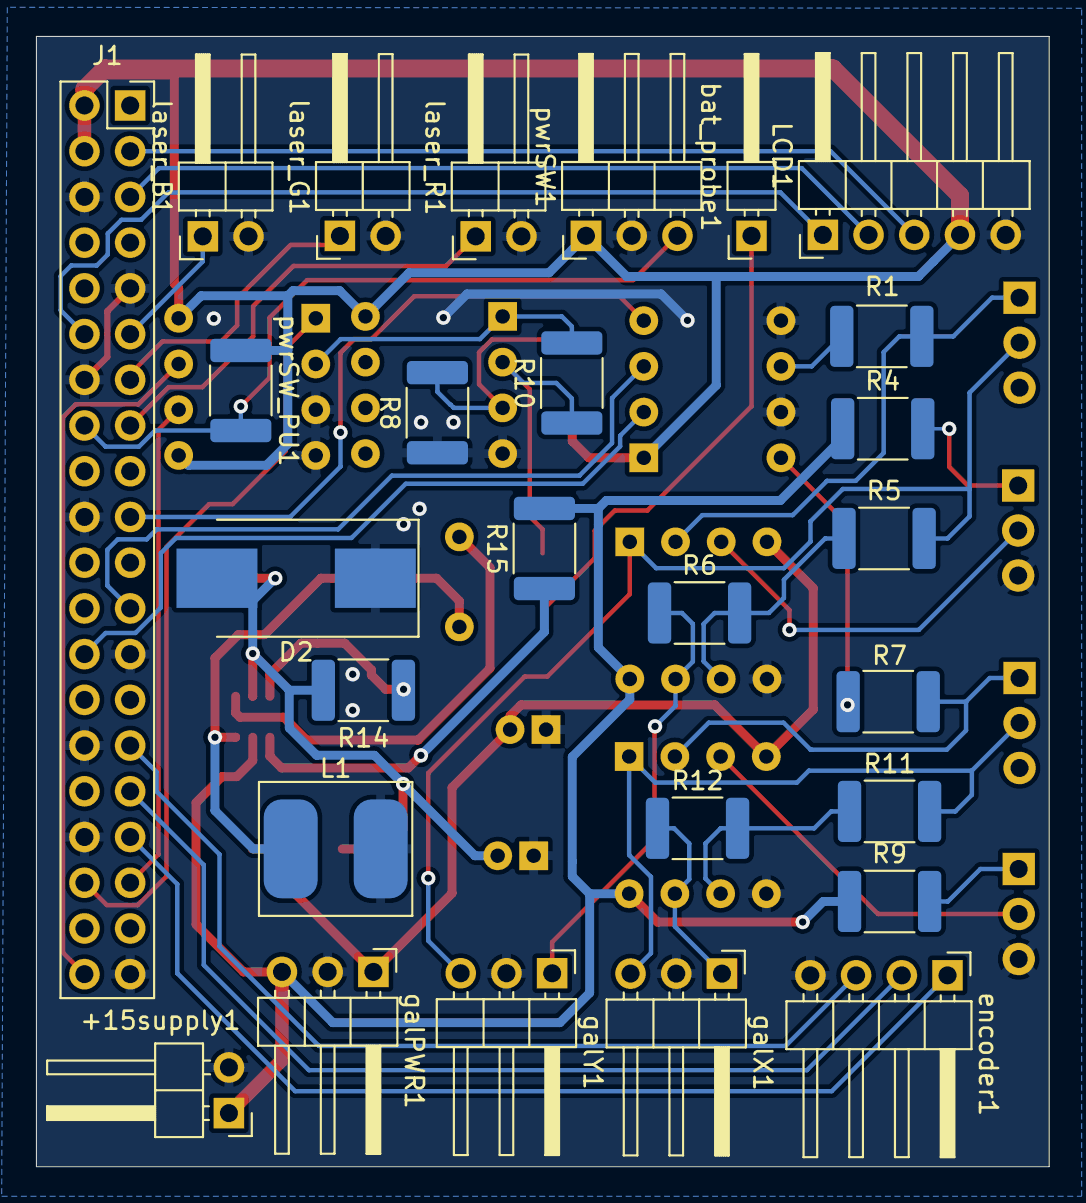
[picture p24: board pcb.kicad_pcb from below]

Board: 2 copper layers, 56.3 x 62.8 mm, 45 parts (27 on the bottom side), 43 nets.

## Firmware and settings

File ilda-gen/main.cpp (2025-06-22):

#include <iostream>
#include <vector>
#include <fstream>
#include <string.h>
#include <math.h>

#include "ildaWriter.h"
#include "font/asteroids_font.h"

class Distance
{
public:
  int32_t x;
  int32_t y;
  int32_t z;

  template <typename T>
  Distance(T from, T to);
};

template <typename T>
Distance::Distance(T from, T to)
{
  this->x = to.x - from.x;
  this->y = to.y - from.y;
  this->z = to.z - from.z;
}

/// @brief
/// @param from
/// @param to
/// @param progress 0-1; the amount of the second color mixed in ie. (0.7 -- 0.3 * from + 0.7 * to
/// @return
RGBColor blendRGBcolors(RGBColor from, RGBColor to, float progress)
{
  return {
      from.r * (1 - progress) + to.r * progress,
      from.g * (1 - progress) + to.g * progress,
      from.b * (1 - progress) + to.b * progress,
  };
};

/// @brief
/// @param from
/// @param to
/// @param progress 0-1; the amount of the second color mixed in ie. (0.7 -- 0.3 * from + 0.7 * to
/// @return
RGBColor blendHSVcolors(HSVColor from, HSVColor to, float progress)
{
  if (to.h > from.h)
  {
    from.h += 360; // ensure that the hue is always increasing
  }
  return hsv2rgb(
      (int)(from.h * (1 - progress) + to.h * progress) % 360,
      from.s * (1 - progress) + to.s * progress,
      from.v * (1 - progress) + to.v * progress);
};

enum line_point_positioning_enum
{
  LINEAR,
  QUADRATIC,
  // EXPONENTIAL,
  SLOW_END // add just a few points near the end of the line to slow the galvos down
};

int16_t blend_coordinate(int16_t from, int32_t distance, uint8_t point_num, uint8_t total_points, line_point_positioning_enum point_positioning)
{
  switch (point_positioning)
  {
  case LINEAR:
    // evenly spaced points
    // std::cout << "dis:" << (float)(point_num * distance / (float)total_points) << std::endl;
    return from + (point_num * distance / (float)total_points);
  default:
    return from; // fallback, should not happen
  }
}

template <typename T>
std::vector<Point>
genLine(T from, T to, uint8_t total_points, line_point_positioning_enum point_positioning, bool omit_first_point = false)
{
  if constexpr (!std::is_same<T, Point>::value && !std::is_same<T, HSVPoint>::value)
  {
    std::cerr << "genLine: T must be Point or HSVPoint" << std::endl;
    exit(1);
  }

  if (!from.laser_on)
  {
    from.color = {0, 0, 0}; // if the laser is off, set the color to black
  }
  if (!to.laser_on)
  {
    to.color = {0, 0, 0}; // if the laser is off, set the color to black
  }

  std::vector<Point> line;
  if (!omit_first_point)
  {
    if constexpr (std::is_same<T, Point>::value == true)
      line.push_back(from);
    else
      line.push_back(Point(
          from.x,
          from.y,
          from.z,
          hsv2rgb(from.color),
          from.laser_on));
    // std::cout << "from: [" << from.x << ", " << from.y << ", " << from.z << "], rgb:" << (int)from.color.r << "," << (int)from.color.g << "," << (int)from.color.b << "," << "laseron:" << from.laser_on << std::endl;
  }

  Distance distance(from, to);
  // std::cout << "distance: " << distance.x << ", " << distance.y << ", " << distance.z << std::endl;

  for (uint8_t i = 1; i < total_points; i++)
  {
    // std::cout << "blend:" << blend_coordinate(from.x, distance.x, i, total_points, point_positioning) << std::endl;

    RGBColor blended_color;
    if constexpr (std::is_same<T, Point>::value == true)
    {
      blended_color = blendRGBcolors(from.color, to.color, (float)i / total_points);
    }
    else
    {
      blended_color = blendHSVcolors(from.color, to.color, (float)i / total_points);
    }

    line.push_back({blend_coordinate(from.x, distance.x, i, total_points, point_positioning),
                    blend_coordinate(from.y, distance.y, i, total_points, point_positioning),
                    blend_coordinate(from.z, distance.z, i, total_points, point_positioning),
                    blended_color,
                    true});
  }

  if constexpr (std::is_same<T, Point>::value == true)
    line.push_back(to);
  else
    line.push_back(Point(
        to.x,
        to.y,
        to.z,
        hsv2rgb(to.color),
        to.laser_on));

  // std::cout << "to: [" << to.x << ", " << to.y << ", " << to.z << "], rgb:" << (int)to.color.r << "," << (int)to.color.g << "," << (int)to.color.b << "," << "laseron:" << to.laser_on << std::endl
  //           << std::endl;
  return line;
}

std::vector<Point> genSineWave(HSVPoint top_left, HSVPoint bottom_right, uint8_t total_points, float x_multi = 2 * 3.14, float phase = 0)
{
  int32_t height = bottom_right.y - top_left.y;
  int32_t width = bottom_right.x - top_left.x;

  std::vector<Point> points;

  for (uint8_t i = 0; i < total_points; i++)
  {
    float progress = (float)i / (total_points - 1);
    int16_t x = top_left.x + progress * width;
    int16_t y = top_left.y + height / 2 + height / 2 * sin(progress * x_multi + phase);

    points.push_back(Point(x,
                           y,
                           top_left.z,
                           hsv2rgb(top_left.color.h, top_left.color.s, top_left.color.v),
                           true));
  }
  return points;
}

std::vector<Point> genRectangle(Point top_left, Point bottom_right, RGBColor color)
{
  std::vector<Point> points;
  std::vector<Point> line;

  line = genLine(Point(top_left.x, top_left.y, 0, color, true),
                 Point(top_left.x, bottom_right.y, 0, color, true),
                 4,
                 LINEAR);
  points.insert(points.end(), line.begin(), line.end());
  line = genLine(Point(top_left.x, bottom_right.y, 0, color, true),
                 Point(bottom_right.x, bottom_right.y, 0, color, true),
                 4,
                 LINEAR);
  points.insert(points.end(), line.begin(), line.end());
  line = genLine(Point(bottom_right.x, bottom_right.y, 0, color, true),
                 Point(bottom_right.x, top_left.y, 0, color, true),
                 4,
                 LINEAR);
  points.insert(points.end(), line.begin(), line.end());
  line = genLine(Point(bottom_right.x, top_left.y, 0, color, true),
                 Point(top_left.x, top_left.y, 0, color, true),
                 4,
                 LINEAR);
  points.insert(points.end(), line.begin(), line.end());

  return points;
}

std::vector<Point> genLetter(char c, Point top_left, Point bottom_right, RGBColor color, Point last_point)
{
  // The source code is in github.com/vst/teensyv/asteroid_font.c and has been compressed to use very little memory in representing the font in memory.
  // The drawing routine extracts the 4-bit X and Y offsets from the array and generates the moveto() or lineto() commands:

  uint8_t c_pos = 255; // default to not found

  for (uint8_t i = 0; i < FONT_NUM_OF_CHARACTERS; i++)
  {
    if (asteroids_font_chars[i] == c)
    {
      c_pos = i;
      break;
    }
  }
  if (c_pos == 255)
  {
    std::cerr << "Character '" << c << "' not found in asteroids font." << std::endl;
    exit(1);
  }

  const uint8_t *const pts = asteroids_font[c_pos].points;
  int next_moveto = 1;
  bool last_moveto = false;

  std::vector<Point> points;

  auto moveto = [&](int16_t x, int16_t y)
  {
    // std::cout << "--moveto: " << x << ", " << y << std::endl;
    Point tmp = Point(x, y, 0, color, false);
    last_point.laser_on = false; // moveto does not turn on the laser
    std::vector<Point> line = genLine(last_point,
                                      tmp,
                                      2,
                                      LINEAR,
                                      false);
    points.insert(points.end(), line.begin(), line.end());
    last_point = tmp;
    last_moveto = true;
  };
  auto lineto = [&](int16_t x, int16_t y)
  {
    //   std::cout << "--lineto: " << x << ", " << y << std::endl;
    Point tmp = Point(x, y, 0, color, true);
    last_point.laser_on = true; // lineto turns on the laser
    std::vector<Point> line = genLine(last_point,
                                      tmp,
                                      2,
                                      LINEAR,
                                      !last_moveto);
    points.insert(points.end(), line.begin(), line.end());
    last_point = tmp;
    last_moveto = false;
  };

  for (int i = 0; i < 8; i++)
  {
    uint8_t delta = pts[i];
    if (delta == FONT_LAST)
      break;
    if (delta == FONT_UP)
    {
      next_moveto = 1;
      continue;
    }

    unsigned dx = ((delta >> 4) & 0xF) * (bottom_right.x - top_left.x) / 8;
    unsigned dy = ((delta >> 0) & 0xF) * (bottom_right.y - top_left.y) / 12;

    if (next_moveto)
      moveto(top_left.x + dx, top_left.y + dy);
    else
      lineto(top_left.x + dx, top_left.y + dy);

    next_moveto = 0;
  }

  return points;
}

/// @brief
/// @param text
/// @param top_left
/// @param bottom_right
/// @param color
/// @param space_width space width relative to the width of a character
/// @param last_point
/// @param skip_last_chars number of characters to not draw at the end of the text
/// @return
std::vector<Point> genText(std::string text, Point top_left, Point bottom_right, RGBColor color, float space_width, Point last_point, uint8_t skip_last_chars = 0)
{
  std::vector<Point> points;
  std::cout << "skip_last_chars: " << (int)skip_last_chars << std::endl;
  for (size_t i = 0; i < text.size(); i++)
  {
    if (text.size() - i - 1 < skip_last_chars)
      continue; // skip the last characters

    char c = text[i];
    uint16_t text_width = bottom_right.x - top_left.x;
    float total_segments = text.size() + (text.size() - 1) * space_width; // number of segments in the text, including spaces

    Point top_left_c = top_left;
    top_left_c.x += (i + i * space_width) * (text_width / total_segments);

    Point bottom_right_c = bottom_right;
    size_t back_i = text.size() - i - 1; // reverse index for the bottom right corner
    bottom_right_c.x -= (back_i + back_i * space_width) * (text_width / total_segments);

    auto letter = genLetter(c, top_left_c, bottom_right_c, color, last_point);
    points.insert(points.end(), letter.begin(), letter.end());
    if (!letter.empty())
      last_point = letter.back();
  }

  if (points.empty())
  {
    std::cout << "empty text, returning last point" << std::endl;
    points.push_back(last_point); // if no points were generated, return the last point
  }

  return points;
}

#define WRITE_SEC                                                         \
  if (sec.points.empty())                                                 \
  {                                                                       \
    sec.points.push_back(Point(ILDA_MIN, ILDA_MIN, 0, {0, 0, 0}, false)); \
  }                                                                       \
  sec.points.back().last_point = 1;                                       \
  sec.number_of_records = endian_switch(sec.points.size());               \
  sections.push_back(sec);

#define INIT_SEC \
  section sec;   \
  sec.frame_number = endian_switch(i);

int main()
{
  std::vector<section> sections;

  for (uint16_t i = 150; i < 400; i++)
  {
    std::cout << "Generating section " << i << std::endl;

    INIT_SEC

    auto last_point = [&](bool turn_off_laser = false)
    {
      if (sec.points.empty())
        if (sections.empty() || sections.back().points.empty())
          return Point(0, 0, 0, {0, 0, 0}, false);
        else
          return Point(sections.back().points.back());

      Point p = Point(sec.points.back());
      if (turn_off_laser)
        p.laser_on = false;
      return p;
    };

    auto letters_appear_skip = [&](uint8_t num_letters, uint16_t first_frame, uint16_t last_frame, uint16_t curr_frame)
    {
      if (curr_frame < first_frame)
      {
        return (uint8_t)num_letters;
      }
      if (curr_frame > last_frame)
      {
        return (uint8_t)0;
      }
      if (first_frame > last_frame)
      {
        std::cerr << "first_frame is greater than last_frame" << std::endl;
        exit(1);
      }

      uint16_t num_frames = last_frame - first_frame;

      float back_progress = (float)(last_frame - curr_frame) / num_frames;

      // std::cout << "back_progress: " << back_progress << std::endl;

      return (uint8_t)(back_progress * num_letters);
    };

    constexpr float START_PERIOD = 3.14 * 8; // period of the sine wave in radians

    if (i == 0)
    {
      sec.points = {Point(ILDA_MIN, ILDA_MIN, ILDA_MIN, {0, 0, 0}, false),
                    Point(ILDA_MAX, ILDA_MAX, ILDA_MAX, {0, 0, 0}, false)};
    }
    if (i < 15)
    {
      float progress = (float)i / 15;

      sec.append(genSineWave(HSVPoint(ILDA_MIN * progress,
                                      ILDA_MIN * progress,
                                      0,
                                      {(0 + 4 * i) % 360, 100, 100},
                                      true),
                             HSVPoint(ILDA_MAX * progress,
                                      ILDA_MAX * progress,
                                      0,
                                      {(180 + 4 * i) % 360, 100, 100},
                                      true),
                             40,
                             START_PERIOD,
                             (float)i / 4));

      sec.append(genLine(last_point(true),
                         Point(ILDA_MIN * progress,
                               0,
                               0,
                               {0, 0, 0},
                               false),
                         2,
                         LINEAR,
                         true));

      // // growing line at the beggining
      // std::vector<Point> line = genLine(HSVPoint(ILDA_MIN * progress,
      //                                            ILDA_MIN * progress,
      //                                            0,
      //                                            {(0 + 4 * i) % 360, 100, 100},
      //                                            true),
      //                                   HSVPoint(ILDA_MAX * progress,
      //                                            ILDA_MAX * progress,
      //                                            0,
      //                                            {(180 + 4 * i) % 360, 100, 100},
      //                                            true),
      //                                   20,
      //                                   LINEAR);
      // sec.points.insert(sec.points.end(), line.begin(), line.end());

      // line = genLine(Point(ILDA_MAX * progress,
      //                      ILDA_MAX * progress,
      //                      0,
      //                      {0, 0, 0},
      //                      false),
      //                Point(ILDA_MIN * progress,
      //                      ILDA_MIN * progress,
      //                      0,
      //                      {0, 0, 0},
      //                      false),
      //                5,
      //                LINEAR);
      // sec.points.insert(sec.points.end(), line.begin(), line.end());
    }
    else if (i < 150)
    {
      sec.append(genSineWave(HSVPoint(ILDA_MIN,
                                      ILDA_MIN,
                                      0,
                                      {(0 + 4 * i) % 360, 100, 100},
                                      true),
                             HSVPoint(ILDA_MAX,
                                      ILDA_MAX,
                                      0,
                                      {(180 + 4 * i) % 360, 100, 100},
                                      true),
                             40,
                             START_PERIOD,
                             (float)i / 4));

      sec.append(genLine(last_point(true),
                         Point(ILDA_MIN,
                               0,
                               0,
                               {0, 0, 0},
                               false),
                         2,
                         LINEAR));

      // // line cycling colors for the rest of the frames
      // std::vector<Point> line = genLine(HSVPoint(ILDA_MIN,
      //                                            ILDA_MIN,
      //                                            0,
      //                                            {(0 + i) % 360, 100, 100},
      //                                            true),
      //                                   HSVPoint(ILDA_MAX,
      //                                            ILDA_MAX,
      //                                            0,
      //                                            {(180 + i) % 360, 100, 100},
      //                                            true),
      //                                   20,
      //                                   LINEAR);
      // sec.points.insert(sec.points.end(), line.begin(), line.end());

      // line = genLine(Point(ILDA_MAX,
      //                      ILDA_MAX,
      //                      0,
      //                      {0, 0, 0},
      //                      false),
      //                Point(ILDA_MIN,
      //                      ILDA_MIN,
      //                      0,
      //                      {0, 0, 0},
      //                      false),
      //                5,
      //                LINEAR);
      // sec.points.insert(sec.points.end(), line.begin(), line.end());
    }
    else if (i < 400) // 300
    {

      uint16_t tunnel_frame = i - 150;
      uint8_t rec_count = 4;
      uint16_t rec_cycle_frames = 60;

      float max_size = -1;
      float min_size = -1;

      for (size_t u = 1; u <= rec_count; u++)
      {
        if ((tunnel_frame + (rec_cycle_frames * u / rec_count)) > rec_cycle_frames)
        {
          float rec_size = ((tunnel_frame + (rec_cycle_frames * u / rec_count)) % rec_cycle_frames) / (float)rec_cycle_frames;

          if (max_size < 0)
          {
            max_size = rec_size;
          }
          else if (rec_size > max_size)
          {
            max_size = rec_size;
          }

          if (min_size < 0)
          {
            min_size = rec_size;
          }
          else if (rec_size < min_size)
          {
            min_size = rec_size;
          }

          std::cout << "rec:" << u << ", size:" << rec_size << std::endl;

          sec.append(genRectangle(Point(ILDA_MIN * rec_size, ILDA_MIN * rec_size, 0, {0, 0, 0}, false),
                                  Point(ILDA_MAX * rec_size, ILDA_MAX * rec_size, 0, {0, 0, 0}, false),
                                  hsv2rgb((int)((1 - rec_size) * 240) % 360, 100, 100)));
          sec.append(last_point(true));
        }
      }

      float center_distance = 0;
      sec.append(Point(0, 0, 0, {0, 0, 0}, false));

      sec.append(genLine(HSVPoint(ILDA_MIN * center_distance, ILDA_MIN * center_distance, 0, {(int)((1 - center_distance) * 240) % 360, 100, 100}, true),
                         HSVPoint(ILDA_MIN * max_size, ILDA_MIN * max_size, 0, {(int)((1 - max_size) * 240) % 360, 100, 100}, true),
                         10,
                         LINEAR,
                         true));
      sec.append(last_point(true));
      sec.append(genLine(last_point(true),
                         Point(0, 0, 0, {0, 0, 0}, false),
                         2,
                         LINEAR,
                         true));
      sec.append(genLine(HSVPoint(ILDA_MAX * center_distance, ILDA_MIN * center_distance, 0, {(int)((1 - center_distance) * 240) % 360, 100, 100}, true),
                         HSVPoint(ILDA_MAX * max_size, ILDA_MIN * max_size, 0, {(int)((1 - max_size) * 240) % 360, 100, 100}, true),
                         10,
                         LINEAR,
                         true));

      sec.append(last_point(true));
      sec.append(genLine(last_point(true),
                         Point(0, 0, 0, {0, 0, 0}, false),
                         2,
                         LINEAR,
                         true));
      sec.append(genLine(HSVPoint(ILDA_MAX * center_distance, ILDA_MAX * center_distance, 0, {(int)((1 - center_distance) * 240) % 360, 100, 100}, true),
                         HSVPoint(ILDA_MAX * max_size, ILDA_MAX * max_size, 0, {(int)((1 - max_size) * 240) % 360, 100, 100}, true),
                         10,
                         LINEAR,
                         true));

      sec.append(last_point(true));
      sec.append(genLine(last_point(true),
                         Point(0, 0, 0, {0, 0, 0}, false),
                         2,
                         LINEAR,
                         true));
      sec.append(genLine(HSVPoint(ILDA_MIN * center_distance, ILDA_MAX * center_distance, 0, {(int)((1 - center_distance) * 240) % 360, 100, 100}, true),
                         HSVPoint(ILDA_MIN * max_size, ILDA_MAX * max_size, 0, {(int)((1 - max_size) * 240) % 360, 100, 100}, true),
                         10,
                         LINEAR,
                         true));
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

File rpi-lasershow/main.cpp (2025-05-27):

#include "ABE_ADCDACPi.h"

#include "zmq.hpp"
#include "lasershow.hpp"
#include "command.hpp"
#include "my_helper.hpp"

#include <string>
#include <filesystem>
#include <fstream>
#include <iostream>
#include <vector>
#include <map>
#include <pigpio.h>

int main()
{
  constexpr uint8_t LASER_PINS[3] = {22, 27, 17};

  for (size_t i = 0; i < 3; i++)
  {
    gpioSetMode(LASER_PINS[i], PI_OUTPUT);
    gpioSetPullUpDown(LASER_PINS[i], PI_PUD_DOWN);
    gpioSetPWMfrequency(LASER_PINS[i], 100000);
    gpioWrite(LASER_PINS[i], 0);
  }

  // Setup ipc communication
  zmq::context_t ctx(1);

  zmq::socket_t publisher(ctx, zmq::socket_type::pub);
  publisher.bind("tcp://*:5556");

  zmq::socket_t command_receiver(ctx, zmq::socket_type::sub);
  command_receiver.bind("tcp://*:5557");
  command_receiver.set(zmq::sockopt::subscribe, "");

  zmq::message_t received;

  options_struct options;
  if (options.loadFromFile(publisher, "./lasershow.cfg"))
  {
    std::cout << "options couldnt be loaded from file" << std::endl;
    publish_message(publisher, "ALERT: options load fail");
  }

  publish_message(publisher, "INFO: lasershow ready");

  IldaReader ildaReader;

  if (gpioInitialise() < 0)
  {
    // pigpio initialisation failed.
    std::cout << "init fail" << std::endl;
    return 1;
  }

  gpioSetMode(SCLK, PI_OUTPUT);
  gpioSetMode(CS, PI_OUTPUT);
  gpioSetMode(MISO, PI_INPUT);

  //needed to set the pins
  std::cout << "start bat_voltage:" << static_cast<int>(bat_raw()) << std::endl;

  bool pass_next_command_read = 0;
  while (true)
  {
    Command command;
    if (!pass_next_command_read)
    {
      // options.project_filename = "";
      command_receiver.recv(received, zmq::recv_flags::none); // blocking
      int exec_val = command.execute(received.to_string(), publisher, options, ildaReader);
      if (exec_val == 1) {
        for (size_t i = 0; i < 3; i++)
        {
          gpioWrite(LASER_PINS[i], 0);
        }
      }
      if (exec_val != 2) 
      {
        continue;
      }
      //else PROJECT
    }
    else
    {
      pass_next_command_read = 0;
    }

    if (lasershow_init(publisher, options, ildaReader) != 0)
    {
      std::cout << "failed to init lasershow" << std::endl;
      publish_message(publisher, "ERROR: failed to init lasershow");
      continue;
    }

    bool first_repeat_or_break = 1;
    while (options.repeat || first_repeat_or_break)
    {
      first_repeat_or_break = 0;
      lasershow_start(publisher, ildaReader, options);

      while (first_repeat_or_break == 0) // also used just as a break flag (if 1 break)
      {
        // maybe receive messages here, then youd need atleast the ildareader(filename) here in main..
        // - no,, just exit the loop lol
        command_receiver.recv(received, zmq::recv_flags::dontwait);
        while (received.size() > 0)
        {
          int exec_val = command.execute(received.to_string(), publisher, options, ildaReader);
          std::cout << "exec_val: " << exec_val << std::endl;
          if (exec_val == 1) // stop
          {
            first_repeat_or_break = 1; // to get out of loop
            for (size_t i = 0; i < 3; i++)
            {
              gpioWrite(LASER_PINS[i], 0);
            }
            break;
          }
          else if (exec_val == 2) // projecting again
          {
            pass_next_command_read = 1; // load a new file and start projecting again
            if (lasershow_init(publisher, options, ildaReader) != 0)
              {
                std::cout << "failed to init lasershow" << std::endl;
                publish_message(publisher, "ERROR: failed to init lasershow");
                first_repeat_or_break = 1; // to get out of loop
                break;
              }
            first_repeat_or_break = 1;
            break;
          }
          else if (exec_val == 3)
          {
            calculate_points(publisher, options, ildaReader);
          }
          command_receiver.recv(received, zmq::recv_flags::dontwait);
        }
        if (first_repeat_or_break == 0)
        {
          // draw, if an error or end of file is reached, break
          int loop_val = lasershow_loop(publisher, options, ildaReader);
          if (loop_val == 2)
            break;
          else if (loop_val == 1)
          {
            options.repeat = 0;
            break;
          }
        }
      }

      if (options.paused == 1) // stopped
        break;
    }
    // lasershow_cleanup(0);
    // publish_message(publisher, "INFO: lasershow cleanup done");
  }
}

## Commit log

2021-12-13 pcb design lvl1
    [pcb.kicad_pcb, pcb.sch]
2021-12-13 cloned https://github.com/tteskac/rpi-lasershow
2021-12-13 pcb half done
2021-12-15 learned how to convert 0-5v to (-10)-(+10)V
2021-12-20 figma pcb designs update
2021-12-20 pcb design exported to svg and png
2021-12-30 wifi manager done
    [anim.blend]
2021-12-30 /home/pi/laser-projector/etc-dnsmasq.conf backup
2022-02-05 backup from pc before switching to ws
2022-04-13 new pcb measurements
2022-04-13 polished new pcb measurements
2022-12-27 add web_ui ilda file select menu
    [pcb.kicad_pcb, pcb.sch]
2022-12-28 change lasershow executable
2022-12-28 change lasershow exec
2023-08-19 start rewriting lasershow to support RGB - define format
2023-10-08 separate encoder.h
2023-10-08 encoder fully supported
2023-10-08 encoder fully supported - fix typo
    [main.cpp]
2023-10-10 FIXED CHANGEVAL and som other things around menu
    [encoder.hpp, main.cpp, menu.hpp]
2023-10-16 fix wiringpi install
2023-10-19 move img to laser_projector-thesis repo
2023-10-23 handle function button presses (not bouncing) +hostpad unit is masked something
2023-10-23 debounce encoder button
2023-10-25 begin work on back button
2023-10-29 BACK BUTTON WOOOOOOOOO
2023-12-08 selection works, but still has bugs
    [main.cpp, menu.hpp]
2023-12-13 encoder to class - before compilation
2023-12-16 rewrite encoder.hpp without a class and add encoder.cpp with static variables
2023-12-16 Revert "Merge branch 'master' of https://github.com/phuid/laser-projector"
    This reverts commit 93da61a8a04ec3b4fb3066d637fb147b8a8e0b32, reversing
    changes made to 8b286b6aca0887c4bed6e5e3f5e220e789c5765d.
    [main.cpp, menu.hpp]
2023-12-17 lasershow comm
2023-12-21 start work on zmq in lasershow exec
2023-12-22 lasershow tak file input
2023-12-23 lasershow comm, start work on options
2023-12-25 fix lasershow PROJECT command + UI comm
    [main.cpp, menu.hpp]
2024-01-07 menu comms fix final (hopefully)
    [main.cpp, menu.hpp]
2024-01-07 pcb, laser_screenshot
    [pcb.kicad_pcb]
2024-01-08 RGB ildareader
    [pcb.kicad_pcb]
2024-01-08 RGB lasershow
2024-01-10 update notes
    [square_white.csv]
2024-01-10 lasershow dont load file on repeat
2024-01-10 fix lasershow errors
2024-01-10 lasershow brightness calc, pwm needed
2024-01-12 fix bug - cleanup before repeat uninits everything and it isnt usable after
    [lasershow.cpp, main.cpp]
2024-01-14 lasershow pigpio
2024-01-14 Revert "UI pigpio"
    This reverts commit b01f6babbd70331cf5474e437a0bcbc8142a7693.
    [config.hpp, encoder.cpp, encoder.hpp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]
2024-01-14 UI back to wiringPi
2024-01-18 start updating web_ui for socket comms (3 terminals)
2024-01-19 pcb done
    [pcb.kicad_pcb]
2024-01-21 pcb todo capacitors
    [pcb.kicad_pcb]
2024-01-21 konzult pcb with tom
    [pcb.kicad_pcb]
2024-01-22 smd pcb done
    [pcb.kicad_pcb]
2024-01-22 rpi power pcb
    [pcb.kicad_pcb]
2024-01-26 finish lasershow lg transition
2024-01-27 gme & laskakit parts
    [kosik.csv, parts.csv]
2024-01-28 pcb silkscreen used pins
    [pcb.kicad_pcb]
2024-01-28 jlc order sent - pcb finished
    [pcb.kicad_pcb]
2024-01-29 add 3d models to kicad
    [pcb.kicad_pcb]
2024-02-02 pigpio lasershow + try trapezoid - still weird + rename helper file
2024-02-02 envelope comms, before lasershow rollback
2024-02-02 lasershow simpler multi receive
2024-02-02 comms complete (on web_ui) with 4 sockets
2024-02-02 lasershow calculate points function
2024-02-02 lasershow option file saving
    [lasershow.cfg]
2024-02-03 lasershow pigpio delayMicros instead of usleep, laser_br calc note in cofig
    [lasershow.cfg]
2024-02-03 lasershow + UI - add "DISPLAY:" for notifications
2024-02-03 UI wiringpi
2024-02-04 3d case,, notes botland paid
2024-02-04 print smlouva
2024-02-04 lasershow scale_up
    [lasershow.cfg]
2024-02-04 recalculate points while projecting
    [lasershow.cfg]
2024-02-04 trapezoid WORKS
    [lasershow.cfg]
2024-02-05 filament ojednat
2024-02-05 web saturate
    [lasershow.cfg]
2024-02-07 vydaje++, 3d soubory
    [Knob_6.3.stl, bat_cover_hold (1).3mf, bat_cover_hold.3mf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]
2024-02-10 some changes to lasershow
    [camera_hold.3mf, low_laser_hold.3mf, newcase_laser_projector v55_side2.3mf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]
2024-02-10 fix lasershow not receiving when projecting - before compile
    [lasershow.cpp]
2024-02-11 ENCODER OVERSHOOT SOLVED?
2024-02-12 web ui settings
    [lasershow.cfg]
2024-02-13 web webing
    [lasershow.cfg]
2024-02-14 settings fux
    [lasershow.cfg]
2024-02-15 web styles
    [lasershow.cfg]
2024-02-15 last updateeasfas
    [lasershow.cfg]
2024-02-16 revert the higher precision point calculation
    [lasershow.cfg]
2024-02-16 proper scale ranges on web
    [lasershow.cfg]
2024-02-17 UI read bat voltage
2024-02-17 bat volt wow
    [lasershow.cfg]
2024-02-17 dont cleanup
    [lasershow.cfg]
2024-02-17 fix UI loop when pressed in display mode
    [lasershow.cfg]
2024-02-17 web stop
    [lasershow.cfg]
2024-02-18 pause resume time hop fixed
    [lasershow.cpp]
2024-02-18 web draw div
    [lasershow.cfg]
2024-02-19 go blue
    [lasershow.cfg]
2024-02-23 add pcb to git
    [pcb-B_Cu.gbr, pcb-B_Mask.gbr, pcb-B_Paste.gbr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]
2024-05-22 discord bot
    [lasershow.cfg]
2025-05-27 how i found it after a year
    [lasershow.cfg]
2025-05-27 how i found pc
    [pcb.kicad_sch]
2025-05-27 working ilda-gen
    [lasershow.cfg]
